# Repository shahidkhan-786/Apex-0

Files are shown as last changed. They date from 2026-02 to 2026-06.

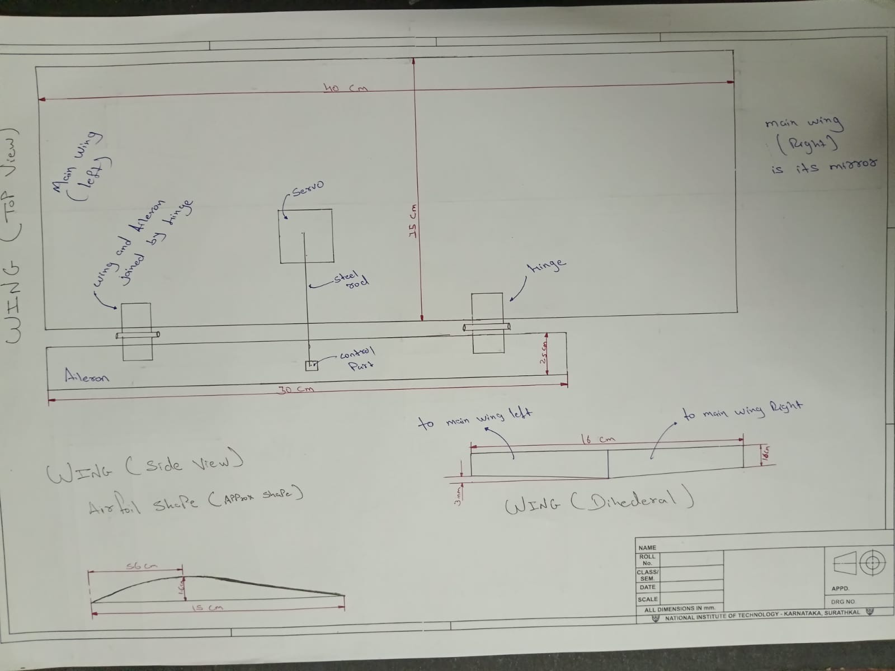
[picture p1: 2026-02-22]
Blueprint/Apex-0 (Part-1).jpeg

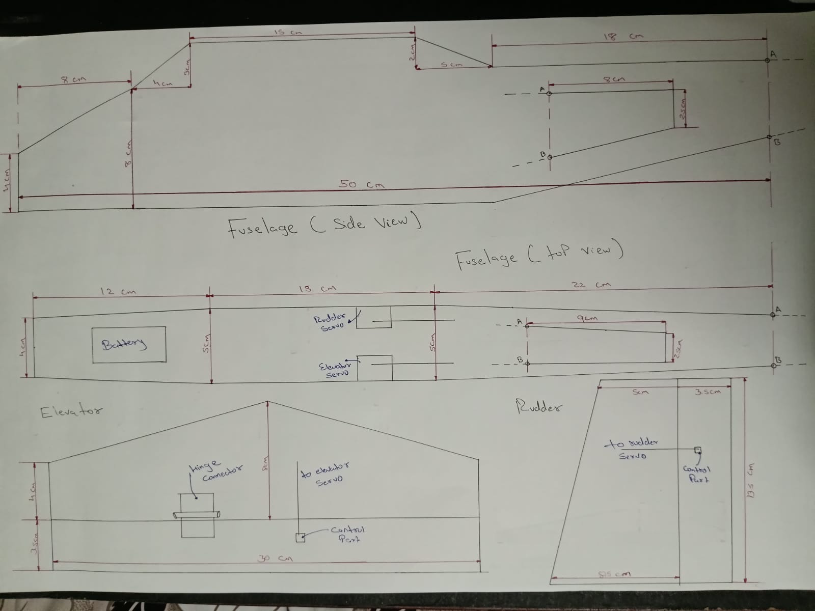
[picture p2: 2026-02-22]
Blueprint/Apex-0 (part-2).jpeg

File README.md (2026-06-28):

# Apex-0

Hello
This Readme is a detailed guide or can say walkthrough of my RC plane making journey.

Apex 0 is a RC trainer plane with 4 control channels.
Made with custom transmitter and reciever.
It will have four controls (Throttle, Ailerons, Rudder and Elevator) 
I will be using ESP32 along with ELRS for communication and controlling servos and throttle.

I am referring to this video : https://youtu.be/LzZ4Oqk_J1Y?si=26B0NShiXBWvZHp2
for structure part...but there was a flaw...The flight time...I have optimized the design for longer flight time.

Also I will be making my own remote controller with 2 Joystick modules.

Since I was little I was amazed by people flying planes and drones, basically all flying stuff. and thats why I wanna make my own plane.

Note that for the first iteration I will be making reciever on a perfboard/zero PCB ...and hence there is no pcb in 3D model.
Reviewers please do not overlook it.

so for the dimensions and proportions you can see my blueprints part where I have showed exact dimensions I will be using.





and for the 3D model you can see my 3D section.









Now for the electronics part :

The transmitter Circuit and PCB : 







and now the reciever part, again note that I am making this on a perfboard and hence there is no layout/routing part :



The BOM screenshots : 





Cart Screenshot (I am ordering froma website called Robu.in) :





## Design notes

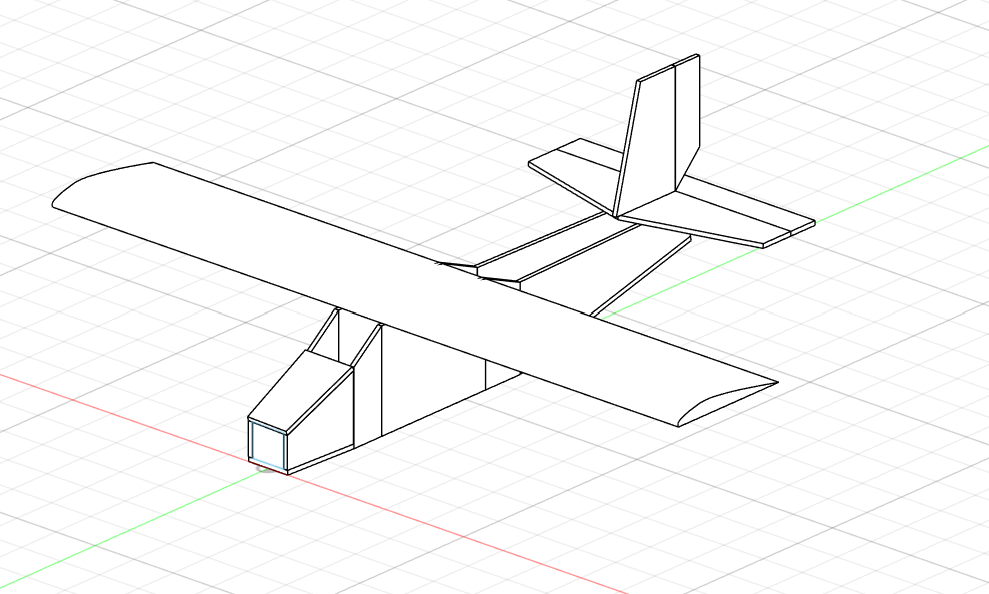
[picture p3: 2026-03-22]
3D files/Screenshot 2026-03-22 143505.png

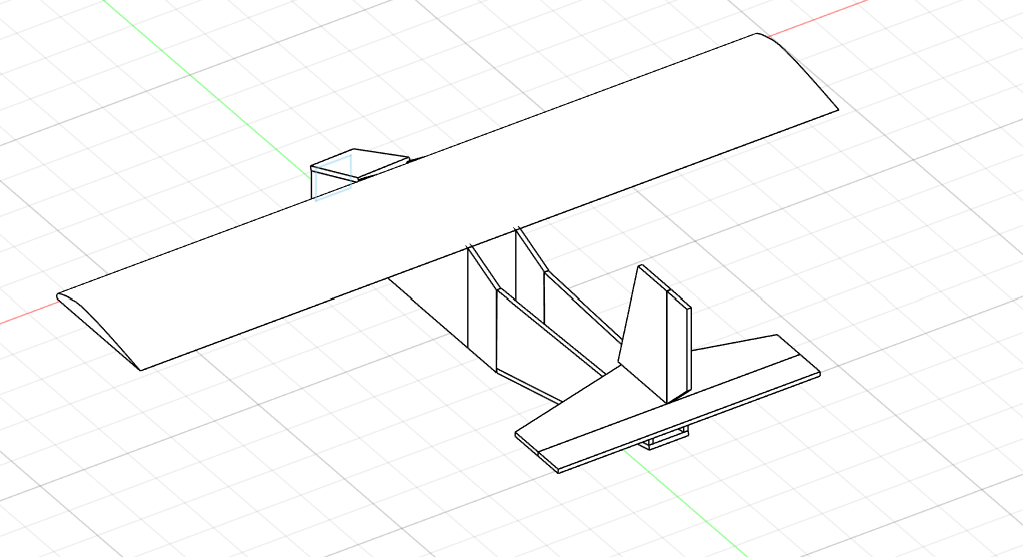
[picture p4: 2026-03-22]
3D files/Screenshot 2026-03-22 143520.png

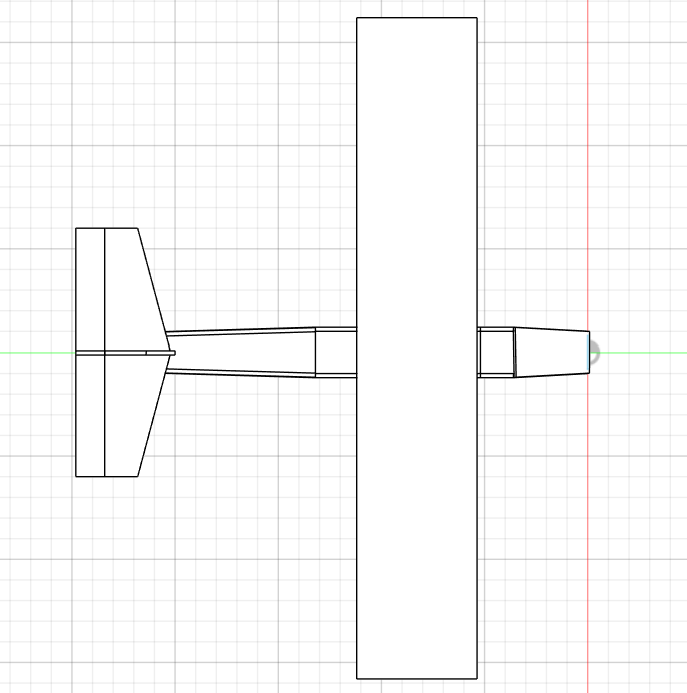
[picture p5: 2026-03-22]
3D files/Screenshot 2026-03-22 143549.png

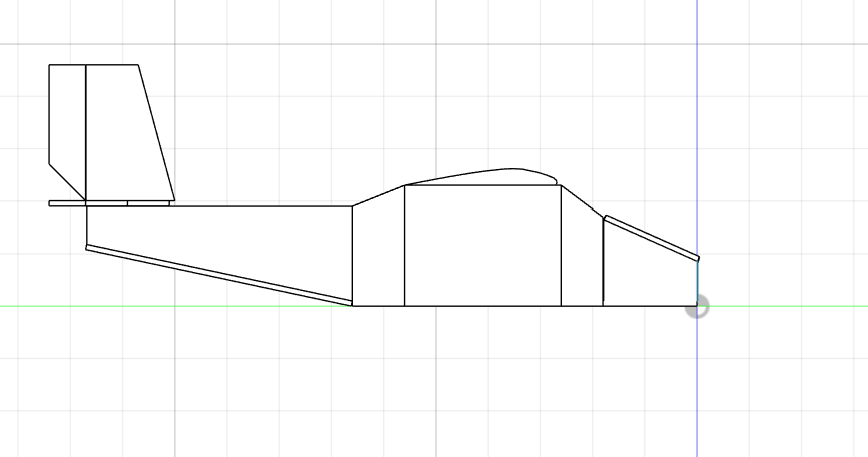
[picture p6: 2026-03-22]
3D files/Screenshot 2026-03-22 143535 - Copy.png

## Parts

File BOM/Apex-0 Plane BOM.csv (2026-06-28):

ITEM | DESCREPTION | QUANTITY | UNIT PRICE (INR) | RUNNING TOTAL (INR) | URL
Foam Board | Main structure | 1 | self sourced | 0 | local shop
Servo motor | MG90S servos | 2 | self sourced | 0 | https://robu.in/product/towardpro-mg90s-mini-digital-servo-2-2kg-0-08sec-13g/
Servo Motor | MG90S servos | 2 | 244 | 488 | https://robu.in/product/towardpro-mg90s-mini-digital-servo-2-2kg-0-08sec-13g/
BLDC Motor | Main motor | 1 | 1257 | 1745 | https://robu.in/product/pro-range-d2207-1500kv-cww-brushless-drone-motor/
BLDC ESC | BLDC ESC | 1 | 1643 | 3388 | https://robu.in/product/emax-blheli-series-30a-esc-oneshot-original/
Propellor | 11inch propellors | 2 | 147 | 3682 | https://robu.in/product/orange-hd-propellers-114711x4-7-abs-1cw1ccw-1pair-black/
ELRS | communication module | 1 | 1375 | 5057 | https://robu.in/product/expresslrs-rx24t-2-4g-receiver/
ESP32 | ESP32 | 1 | 409 | 5466 | https://robu.in/product/esp-wroom-32-wifi-bluetooth-networking-smart-component-development-board/
Battery | 11.1V 1800mAH LiPo | 1 | 1773 | 7239 | https://robu.in/product/orange-11-1v-1800mah-3s-40c-lipo-battery-pack-xt60-connector/
Buck converter | 5V supply | 2 | 175 | 7589 | https://robu.in/product/dc-dc-step-down-buck-converter-power-supply-module-24v-12v-9v-to-5v-5a-25w-replace-lm2596s/
 |  | Grand total (INR) | 7589
 |  | Grand total (USD) | 81

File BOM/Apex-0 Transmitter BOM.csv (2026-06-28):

ITEM | DESCREPTION | QUANTITY | UNIT PRICE (INR) | RUNNING TOTAL (INR) | URL
ESP32 | ESP32 | 1 | 409 | 409 | https://robu.in/product/esp-wroom-32-wifi-bluetooth-networking-smart-component-development-board/
OLED display | Oled display | 1 | 209 | 618 | https://robu.in/product/0-96-oled-display-module/
ELRS | communication module | 1 | 1375 | 1993 | https://robu.in/product/expresslrs-rx24t-2-4g-receiver/
Joystick module | Joysticks | 2 | self sourced
Potentiometer | potentiometer | 1 | self sourced
PCB | main PCB to hold everything | 5(Minimum) | 2138 | 4131 | https://robu.in
 |  | Grand total (INR) | 4131
 |  | Grand total (USD) | 44

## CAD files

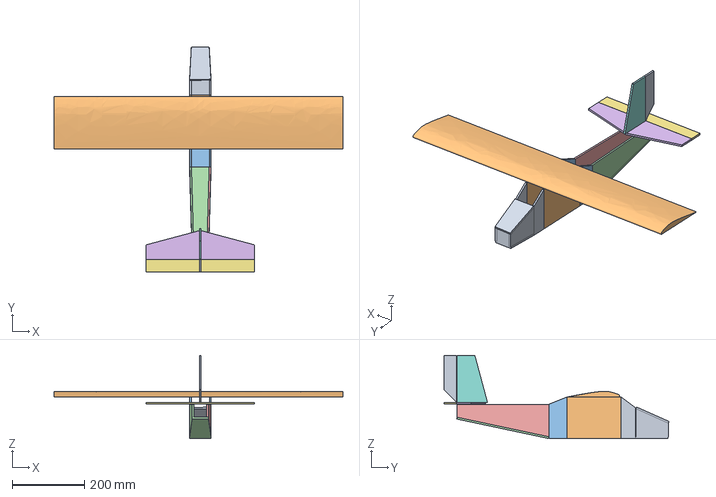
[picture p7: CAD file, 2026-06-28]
3D files/Apex 0.step
800.0 x 622.6 x 230.2 mm

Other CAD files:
3D files/Apex 0 Rough 3D Model.stl
3D files/Apex 0.f3z

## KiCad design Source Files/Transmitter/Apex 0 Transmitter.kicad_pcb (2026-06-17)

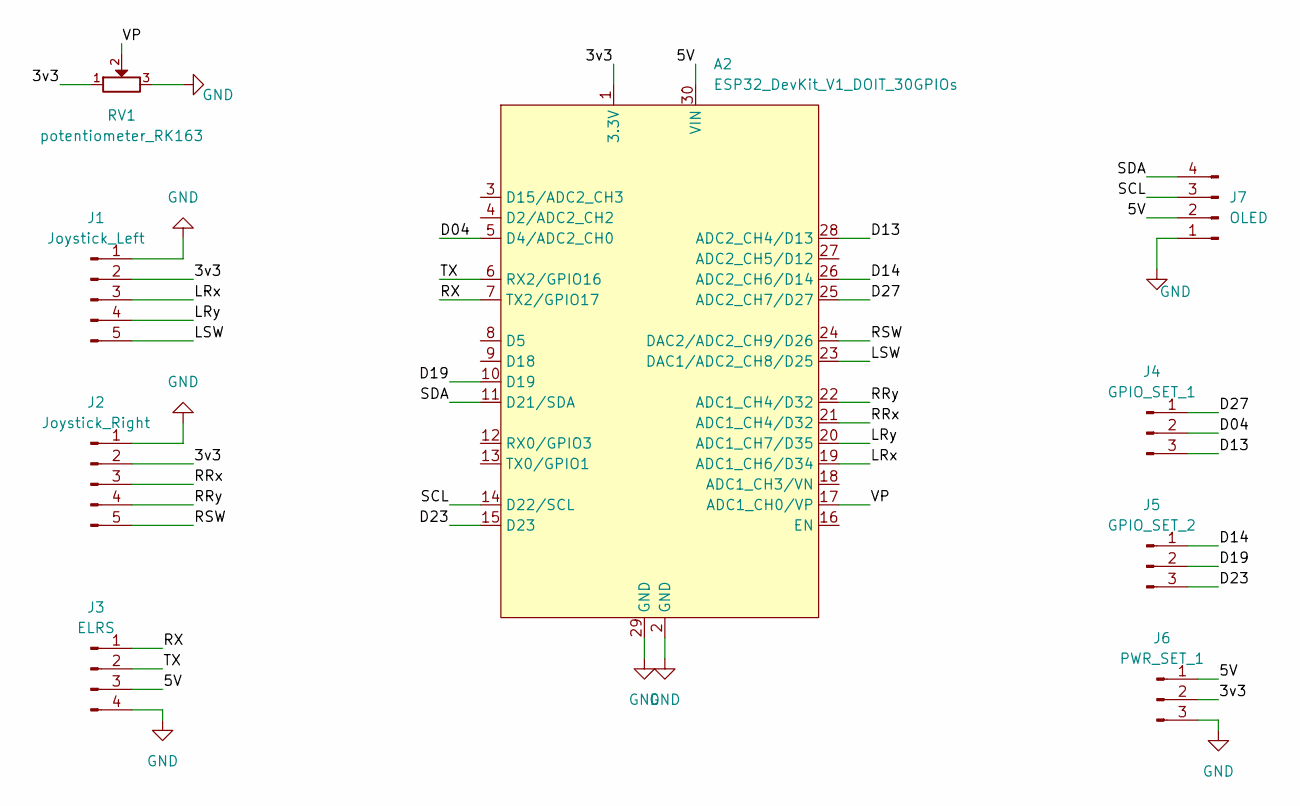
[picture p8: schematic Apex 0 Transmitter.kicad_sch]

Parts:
A2: ESP32_DevKit_V1_DOIT_30GPIOs; DOIT_ESP32_DEVKIT_30Pins
J1: Joystick_Left; PinHeader_1x05_P2.54mm_Vertical
J2: Joystick_Right; PinHeader_1x05_P2.54mm_Vertical
J3: ELRS; PinHeader_1x04_P2.54mm_Vertical
J4: GPIO_SET_1; PinHeader_1x03_P2.54mm_Vertical
J5: GPIO_SET_2; PinHeader_1x03_P2.54mm_Vertical
J6: PWR_SET_1; PinHeader_1x03_P2.54mm_Vertical
J7: OLED; PinHeader_1x04_P2.54mm_Vertical
RV1: potentiometer_RK163; Potentiometer_Alps_RK163_Single_Horizontal

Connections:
/3v3: A2.1 (3.3V), J1.2, J2.2, J6.2, RV1.1
/5V: A2.30 (VIN), J3.3, J6.1, J7.2
/D04: A2.5 (D4/ADC2_CH0), J4.2
/D13: A2.28 (ADC2_CH4/D13), J4.3
/D14: A2.26 (ADC2_CH6/D14), J5.1
/D19: A2.10 (D19), J5.2
/D23: A2.15 (D23), J5.3
/D27: A2.25 (ADC2_CH7/D27), J4.1
/LRx: A2.19 (ADC1_CH6/D34), J1.3
/LRy: A2.20 (ADC1_CH7/D35), J1.4
/LSW: A2.23 (DAC1/ADC2_CH8/D25), J1.5
/RRx: A2.21 (ADC1_CH4/D32), J2.3
/RRy: A2.22 (ADC1_CH4/D32), J2.4
/RSW: A2.24 (DAC2/ADC2_CH9/D26), J2.5
/RX: A2.7 (TX2/GPIO17), J3.1
/SCL: A2.14 (D22/SCL), J7.3
/SDA: A2.11 (D21/SDA), J7.4
/TX: A2.6 (RX2/GPIO16), J3.2
/VP: A2.17 (ADC1_CH0/VP), RV1.2
GND: A2.2 (GND), A2.29 (GND), J1.1, J2.1, J3.4, J6.3, J7.1, RV1.3

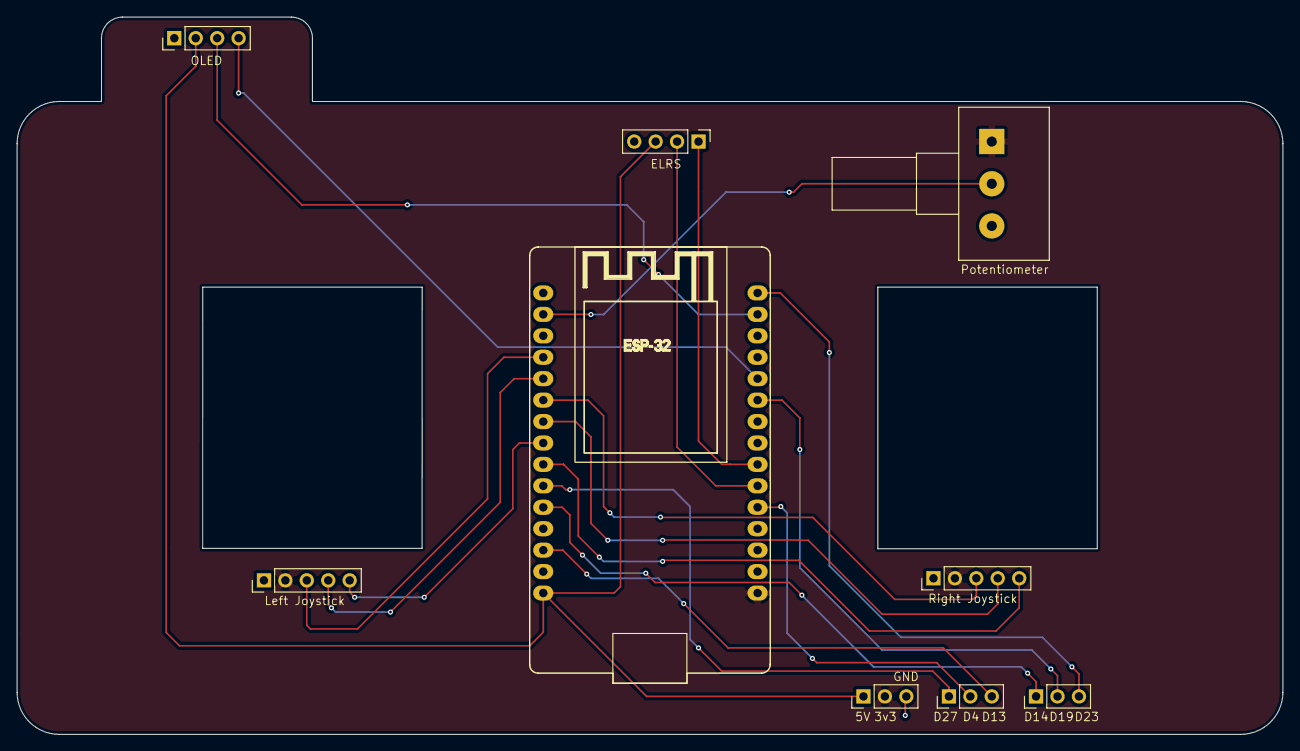
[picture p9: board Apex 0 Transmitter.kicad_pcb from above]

Board: 2 copper layers, 150.0 x 85.0 mm, 9 parts (0 on the bottom side), 20 nets.

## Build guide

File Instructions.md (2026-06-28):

for the actual modelling or making part, first we start by cutting the foam board in dimensions in blueprint.
for cutting, since foam board is soft, we can easily do it with a cutter...not much of a hassle.
just make sure that the aerofoil shape is not altered for left snd right parts, otherwise plane can become unstable.

so after cutting we will join and parts and give it the shape of a plane...for that you can see 3D files...for how each part joins
and which part joins to what...for joining I will be using superglue and hot glue gun...as they are fast and effecient.
since it is a foamboard, typical screws won't work.

now for the servos attachment...the ailerons servos would be attached inside the left and right wings respectively and elevator and rudder 
will be inside the plane to balance centre of gravity...exact placement will be updated after parts arrive.

also for the hinges we will make a typical V-cut...it allows both strength and movement...and then apply silicone hinge.
if you see the youtube video I referenced to, you will gget to know.

and the thrust motor, that will be attached at the nose, the holes for it will depend on which motor you use.

a thing to worth note is that we should put the communication module or atleast its antinnea should be out of the frame for
maximum range. and the imu should be in the geometric center of the plane...I think it will be around near middle of the wing to trailing edge 
of the wing. again the exact placement and other things will be mentioned after parts arrive...also there will be journals.

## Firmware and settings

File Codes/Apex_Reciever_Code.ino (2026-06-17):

/*
 * APEX 0 - DIY Flight Control Autopilot Software
 * Developed for Hack Club Macondo Project
 * * Target MCU: ESP32 30-Pin DevKit
 * Mappings perfectly matched to Final Receiver Perfboard Layout
 */

#include <Wire.h>
#include <Adafruit_MPU6050.h>
#include <Adafruit_Sensor.h>

// --- Hardware Pin Definitions ---
#define PIN_UART_RX2     16 // Connected to ELRS TX Pad
#define PIN_UART_TX2     17 // Connected to ELRS RX Pad

#define PIN_PWM_THROTTLE 25 // J1: ESC Command
#define PIN_PWM_AIL_L    26 // J2: Left Aileron Servo
#define PIN_PWM_AIL_R    27 // J3: Right Aileron Servo
#define PIN_PWM_ELEVATOR 14 // J4: Elevator Servo
#define PIN_PWM_RUDDER   13 // J5: Rudder Servo

// --- LEDC Hardware PWM Channel Configuration ---
#define PWM_FREQ         50    // Standard analog servo frequency (50Hz)
#define PWM_RESOLUTION   16    // 16-bit resolution tracking (0 to 65535)

// 50Hz period = 20ms. 
// 1ms pulse width (Min RC range)  = (1ms / 20ms) * 65535 = 3276
// 1.5ms pulse width (Center)      = (1.5ms / 20ms) * 65535 = 4915
// 2ms pulse width (Max RC range)  = (2ms / 20ms) * 65535 = 6553

#define RC_MIN_DUTY      3276
#define RC_CEN_DUTY      4915
#define RC_MAX_DUTY      6553

// Define independent internal hardware generation timers
#define CH_THROTTLE      0
#define CH_AIL_L         1
#define CH_AIL_R         2
#define CH_ELEVATOR      3
#define CH_RUDDER        4

// --- Core Autopilot System Variables ---
Adafruit_MPU6050 mpu;
int16_t channels[4] = {1500, 1500, 1000, 1500}; // Roll, Pitch, Throttle, Yaw Defaults

// --- PID Control Variable Structures ---
float roll_error = 0, pitch_error = 0;
float roll_pwm_output = 0, pitch_pwm_output = 0;

// PID Tunings (Configured for standard foam park-fliers; adjustable post-flight trials)
float Kp = 1.2;
float Ki = 0.05;
float Kd = 0.4;

void setup() {
    Serial.begin(115200);
    
    // Initialize ExpressLRS UART2 Stream Data Port
    Serial2.begin(416666, SERIAL_8N1, PIN_UART_RX2, PIN_UART_TX2);
    
    // Initialize MPU6050 / 10DOF Frame Interface 
    if (!mpu.begin()) {
        Serial.println("MPU6050 baseline connection offline. Proceeding in testing bypass mode.");
    } else {
        mpu.setAccelerometerRange(MPU6050_RANGE_4_G);
        mpu.setGyroRange(MPU6050_RANGE_250_DEG);
        mpu.setFilterBandwidth(MPU6050_BAND_21_HZ);
    }
    
    // Configure ESP32 LEDC Timers & Pins for Servos & Motor Outputs
    ledcSetup(CH_THROTTLE, PWM_FREQ, PWM_RESOLUTION);
    ledcAttachPin(PIN_PWM_THROTTLE, CH_THROTTLE);
    
    ledcSetup(CH_AIL_L, PWM_FREQ, PWM_RESOLUTION);
    ledcAttachPin(PIN_PWM_AIL_L, CH_AIL_L);
    
    ledcSetup(CH_AIL_R, PWM_FREQ, PWM_RESOLUTION);
    ledcAttachPin(PIN_PWM_AIL_R, CH_AIL_R);
    
    ledcSetup(CH_ELEVATOR, PWM_FREQ, PWM_RESOLUTION);
    ledcAttachPin(PIN_PWM_ELEVATOR, CH_ELEVATOR);
    
    ledcSetup(CH_RUDDER, PWM_FREQ, PWM_RESOLUTION);
    ledcAttachPin(PIN_PWM_RUDDER, CH_RUDDER);
    
    // Safe-Start Initialization (Force Throttle Low to avoid motor accidental spooling)
    ledcWrite(CH_THROTTLE, RC_MIN_DUTY);
}

void loop() {
    // 1. Check for Incoming CRSF Packets from ELRS Module
    if (Serial2.available() >= 26) {
        if (Serial2.read() == 0xC8) { // Locate CRSF Sync Start Byte
            uint8_t buffer[25];
            Serial2.readBytes(buffer, 25);
            
            if (buffer[1] == 0x16) { // Verify Channels Frame Type
                // Decode packed 11-bit chunks back into regular raw channel integer metrics
                channels[0] = ((buffer[2] | buffer[3] << 8) & 0x07FF);        // Roll Channel
                channels[1] = ((buffer[3] >> 3 | buffer[4] << 5) & 0x07FF);   // Pitch Channel
                channels[2] = ((buffer[4] >> 6 | buffer[5] << 2 | buffer[6] << 10) & 0x07FF); // Throttle
                channels[3] = ((buffer[6] >> 1 | buffer[7] << 7) & 0x07FF);   // Yaw Channel
            }
        }
    }
    
    // 2. Fetch Inertial Readouts from the IMU
    sensors_event_t a, g, temp;
    mpu.getEvent(&a, &g, &temp);
    
    // Calculate simple Euler angles from raw IMU metrics (Complementary Filter Skeleton)
    float pitch_actual = (atan2(a.acceleration.y, a.acceleration.z) * 180.0) / M_PI;
    float roll_actual  = (atan2(a.acceleration.x, a.acceleration.z) * 180.0) / M_PI;
    
    // Convert stick data to target angles (-30 to +30 degrees bank limits)
    float roll_target  = map(channels[0], 172, 1811, -30, 30);
    float pitch_target = map(channels[1], 172, 1811, -30, 30);
    
    // 3. Execution of Autonomous PID Stability Loop calculations
    roll_error = roll_target - roll_actual;
    pitch_error = pitch_target - pitch_actual;
    
    roll_pwm_output  = roll_error * Kp;   // Basic Proportional stabilization response
    pitch_pwm_output = pitch_error * Kp;
    
    // 4. Actuator Mixer Engine Map Matrix
    // Map intermediate calculation metrics straight back down to standard LEDC Hardware Outputs
    long throttle_duty = map(channels[2], 172, 1811, RC_MIN_DUTY, RC_MAX_DUTY);
    long rudder_duty   = map(channels[3], 172, 1811, RC_MIN_DUTY, RC_MAX_DUTY);
    
    long ail_l_duty    = RC_CEN_DUTY + (roll_pwm_output * 50); // Direct Differential Mix
    long ail_r_duty    = RC_CEN_DUTY - (roll_pwm_output * 50); // Ailerons act in opposite orientations
    long elevator_duty = RC_CEN_DUTY + (pitch_pwm_output * 50);
    
    // Enforce bounds protection clips to avoid mechanically stripping micro servo gears
    ail_l_duty    = constrain(ail_l_duty, RC_MIN_DUTY, RC_MAX_DUTY);
    ail_r_duty    = constrain(ail_r_duty, RC_MIN_DUTY, RC_MAX_DUTY);
    elevator_duty = constrain(elevator_duty, RC_MIN_DUTY, RC_MAX_DUTY);
    
    // Write out the mixed calculations straight to the physical hardware pins
    ledcWrite(CH_THROTTLE, throttle_duty);
    ledcWrite(CH_AIL_L, ail_l_duty);
    ledcWrite(CH_AIL_R, ail_r_duty);
    ledcWrite(CH_ELEVATOR, elevator_duty);
    ledcWrite(CH_RUDDER, rudder_duty);
    
    delay(10); // High performance, low latency fixed 100Hz autopilot update execution loop
}

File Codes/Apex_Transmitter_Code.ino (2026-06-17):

/*
 * APEX 0 - DIY ExpressLRS Radio Transmitter Handset
 * Developed for Hack Club Macondo Project
 * * Target MCU: ESP32 30-Pin DevKit
 * Mappings perfectly matched to Final Transmitter Schematic
 */

#include <Wire.h>
#include <Adafruit_GFX.h>
#include <Adafruit_SSD1306.h>

// --- Hardware Pin Definitions ---
#define PIN_JOY_LEFT_X  34  // LRx (ADC1)
#define PIN_JOY_LEFT_Y  35  // LRy (ADC1)
#define PIN_SWITCH_LEFT 25  // LSW (Digital Input)

#define PIN_JOY_RIGHT_X 32  // RRx (ADC1)
#define PIN_JOY_RIGHT_Y 33  // RRy (ADC1)
#define PIN_SWITCH_RIGHT 26 // RSW (Digital Input)

#define PIN_POT_AUX     36  // VP (ADC1 Tuning Potentiometer)

#define PIN_UART_TX2    17  // Connected to ELRS RX Pad
#define PIN_UART_RX2    16  // Connected to ELRS TX Pad

// --- OLED Configuration ---
#define SCREEN_WIDTH 128
#define SCREEN_HEIGHT 64
Adafruit_SSD1306 display(SCREEN_WIDTH, SCREEN_HEIGHT, &Wire, -1);

// --- CRSF Frame Structures ---
#define CRSF_START_BYTE     0xC8
#define CRSF_FRAMETYPE_RC_CHANNELS 0x16

struct CrsfChannels {
    unsigned int ch0 : 11;
    unsigned int ch1 : 11;
    unsigned int ch2 : 11;
    unsigned int ch3 : 11;
    unsigned int ch4 : 11;
    unsigned int ch5 : 11;
    unsigned int ch6 : 11;
    unsigned int ch7 : 11;
    unsigned int ch8 : 11;
    unsigned int ch9 : 11;
    unsigned int ch10 : 11;
    unsigned int ch11 : 11;
    unsigned int ch12 : 11;
    unsigned int ch13 : 11;
    unsigned int ch14 : 11;
    unsigned int ch15 : 11;
} __attribute__((packed));

uint8_t crsfPacket[26];

// --- CRC8 Calculation Function for ExpressLRS ---
uint8_t crsf_crc8(const uint8_t *ptr, uint8_t len) {
    uint8_t crc = 0;
    while (len--) {
        crc ^= *ptr++;
        for (uint8_t i = 0; i < 8; i++) {
            if (crc & 0x80) {
                crc = (crc << 1) ^ 0xD5;
            } else {
                crc <<= 1;
            }
        }
    }
    return crc;
}

void setup() {
    // Initialize Debug Console
    Serial.begin(115200);
    
    // Initialize Hardware UART2 for ExpressLRS Module at native CRSF Speed
    Serial2.begin(416666, SERIAL_8N1, PIN_UART_RX2, PIN_UART_TX2);
    
    // Configure Switches with internal pullups
    pinMode(PIN_SWITCH_LEFT, INPUT_PULLUP);
    pinMode(PIN_SWITCH_RIGHT, INPUT_PULLUP);
    
    // Initialize I2C OLED Screen
    if(!display.begin(SSD1306_SWITCHCAPVCC, 0x3C)) {
        Serial.println(F("OLED allocation failed"));
    } else {
        display.clearDisplay();
        display.setTextSize(1);
        display.setTextColor(SSD1306_WHITE);
        display.setCursor(0,0);
        display.println("  APEX 0 TX ONLINE  ");
        display.println("   HACKCLUB MACONDO ");
        display.display();
    }
}

void loop() {
    // 1. Read Analog Joysticks and Pot (ESP32 12-bit ADC: 0 to 4095)
    int raw_roll     = analogRead(PIN_JOY_RIGHT_X);
    int raw_pitch    = analogRead(PIN_JOY_RIGHT_Y);
    int raw_throttle = analogRead(PIN_JOY_LEFT_Y);
    int raw_yaw      = analogRead(PIN_JOY_LEFT_X);
    int raw_aux      = analogRead(PIN_POT_AUX);
    
    // 2. Map values to standard ExpressLRS channel limits (CRSF ranges from 172 to 1811)
    // Center point is 992. Equivalent to standard 1000us - 2000us servo signals.
    uint16_t crsf_roll     = map(raw_roll,     0, 4095, 172, 1811);
    uint16_t crsf_pitch    = map(raw_pitch,    0, 4095, 172, 1811);
    uint16_t crsf_throttle = map(raw_throttle, 0, 4095, 172, 1811);
    uint16_t crsf_yaw      = map(raw_yaw,      0, 4095, 172, 1811);
    uint16_t crsf_aux      = map(raw_aux,      0, 4095, 172, 1811);
    
    uint16_t sw_l = (digitalRead(PIN_SWITCH_LEFT) == LOW) ? 1811 : 172;
    uint16_t sw_r = (digitalRead(PIN_SWITCH_RIGHT) == LOW) ? 1811 : 172;

    // 3. Assemble the CRSF Serialization Packet Array
    crsfPacket[0] = CRSF_START_BYTE;
    crsfPacket[1] = 24; // Packet Payload Length
    crsfPacket[2] = CRSF_FRAMETYPE_RC_CHANNELS;
    
    CrsfChannels *channels = (CrsfChannels *)&crsfPacket[3];
    channels->ch0 = crsf_roll;
    channels->ch1 = crsf_pitch;
    channels->ch2 = crsf_throttle;
    channels->ch3 = crsf_yaw;
    channels->ch4 = sw_l;
    channels->ch5 = sw_r;
    channels->ch6 = crsf_aux;
    
    // Calculate Checksum over payload and payload header type
    crsfPacket[25] = crsf_crc8(&crsfPacket[2], 23);
    
    // 4. Stream data frame down the serial pipeline directly to the ELRS module
    Serial2.write(crsfPacket, 26);
    
    // 5. Refresh OLED Telemetry Screen Layout at a clean 10Hz pace
    static unsigned long lastUpdate = 0;
    if (millis() - lastUpdate > 100) {
        lastUpdate = millis();
        display.clearDisplay();
        display.setCursor(0,0);
        display.println("--- APEX 0 LINK ---");
        display.printf("THR: %d\n", map(crsf_throttle, 172, 1811, 0, 100));
        display.printf("RLL: %d | PTH: %d\n", map(crsf_roll, 172, 1811, -50, 50), map(crsf_pitch, 172, 1811, -50, 50));
        display.printf("AUX POT: %d\n", map(crsf_aux, 172, 1811, 0, 100));
        display.println("STATUS: WAITING RX...");
        display.display();
    }
    
    delay(20); // Balanced 50Hz control loop interval
}

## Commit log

2026-02-22 Main Blueprint
    These are the main Schematic I will be using for the build.
2026-02-22 Add files via upload
    This is screenshot of my BOM
2026-03-22 These are the 3D files required
    These are Rough (Yet most finished) models...you have to place holes according to your screw needs and also motor mounts according to your motor sizes.
    I have made the sketch in Blueprint folder where can you place motor mounts according to your motor and needs
    [Apex 0 Rough 3D Model.stl, Apex 0 Rough 3D Model.stp]
2026-03-24 Add receiver code for RF24 radio and servos
2026-03-24 Add note about ESP32 version differences
2026-03-25 This is BOM for the project
    [Apex-0 BOM.csv]
2026-03-25 Update README with Bill of Materials and images
    Added Bill of Materials section and updated images.
2026-05-18 Revise README for Apex 0 RC plane project
    Updated the README to enhance clarity and detail about the RC plane project, including transmitter and receiver schematics.
2026-05-21 Update README with notes on circuit design and PCB
    Added a note about using perfboard for the first iteration and clarified the absence of a PCB in the 3D model.
2026-05-31 Add project transfer notes for material
    Document project transfer history and reasons.
2026-06-17 BOM Screenshot
2026-06-17 Enhance README with project motivation and images
    Added personal motivation and details about the project, including the BOM and cart screenshots.
2026-06-18 Update BOM with new items and totals
    [Apex-0 BOM.csv]
2026-06-27 Transmitter Gerber
2026-06-28 Expand instructions for foam board plane assembly
    Added detailed instructions for assembling a foam board model plane, including cutting, joining parts, servo attachment, hinge creation, and placement of components.
2026-06-28 Fix BOM screenshot reference and add new images
    Updated the README to correct the BOM screenshot reference and added additional screenshots.
